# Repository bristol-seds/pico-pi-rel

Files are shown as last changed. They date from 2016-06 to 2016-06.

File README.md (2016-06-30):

# pico-pi

This repository contains the source and hardware for a High Altitude
Balloon (HAB) tracker based around a
[Raspberry Pi Zero](https://www.raspberrypi.org/products/pi-zero/). The
Pi Zero V1.3 includes a camera connector, so we can use a
[Sony IMX219 camera](https://uk.farnell.com/raspberry-pi/rpi-8mp-camera-board/raspberry-pi-camera-board-v2/dp/2510728)
to return live images.

This design is optimised for weight-constrained payloads that use
solar panels for power. If you're new to HAB or using a Latex weather
balloon, then check out the awesome
[Pi in the Sky](http://www.pi-in-the-sky.com) project instead!

# Hardware

[README.md](hw/README.md)

# Mass Budget

| Part | Mass |
| ---  | --- |
| Raspberry Pi Zero V1.3 | 9g |
| Raspberry Pi Camera | 3.5g |
| [5F Supercap](http://www.farnell.com/datasheets/1640988.pdf) | 7g |
| Solar panels to supply 400mA @ 4.8V | 15.2g |
| [pico-pi hardware](hw/) | 8g |
| Thermal insulation | 3g |
| Wire for antennas | 3g |

Current Total: `48.7g`
Target: `50g`

# License

[MIT](LICENSE.md)

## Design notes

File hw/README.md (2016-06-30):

# Hardware for pico-pi

The folder contains the schematic files for the pico-pi header
board. This provides us with the all the additional hardware
functionality we need for a balloon tracker.

* 868MHz RFM96W LoRa Radio
* u-Blox MAX-M8Q GPS
* 144MHz and 434MHz Radios
* Microcontroller to act as watchdog
* Input diodes for solar panels
* optional ADXL345 accelerometer

_[Schematics](pico-pi.sch.pdf)_

_[Board Drawings](pico-pi.kicad_pcb.pdf)_

_[3D Rendering](pico-pi.kicad_pcb.png)_

_[Gerbers](gerbers/)_

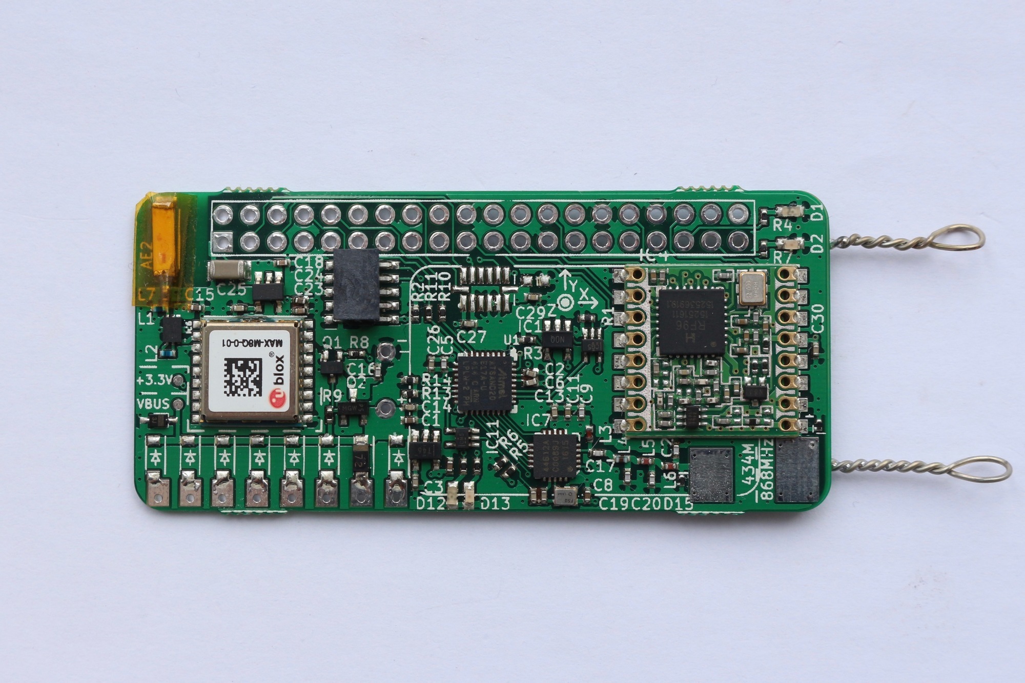
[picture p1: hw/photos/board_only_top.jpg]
Assembled pico-pi header board


# Design Features

## GPS Amplifier + Antenna

We include a GPS
[Front End](http://www.infineon.com/dgdl/bgm1034N7.pdf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)
and a
[Chip Antenna](http://www.johansontechnology.com/datasheets/antennas/1575AT43A0040.pdf). This
choice of antenna trades off sensitivity for low mass, while the Front
End mantains sufficient sensitivity and noise rejection.

## Power Conditioning

Pi Zero uses a
[PAM2306](http://www.mouser.com/ds/2/115/PAM2306-336770.pdf) for
power. Specifically it uses the KE variant for both 1.8V and 3.3V
outputs. The camera supply comes from this 3.3V line.

We can reduce the voltage on the 5V net to about 3.5V as we're not
using either the HDMI or USB sockets. This avoids having to include a
boost regulator, which saves cost and complexity.

A [supercapacitor](http://www.farnell.com/datasheets/1640988.pdf)
prevents voltage droop and brown-out in periods of high demand or
momentary solar panel shadowing. This allows us to use fewer solar
panels, and means we don't need to profile maximum current
consumption.

The Atmel SAMD20 microcontroller enables power to the rest of the
system, and also acts as watchdog. The GPS and RFM95W radio are
supplied by their own 3.3V LDO to reduce the load on the pi zero buck.

## ADXL345

Accelerometer data might be useful, in particular it will give us
pitch when taking photos. Could also be processed to quantify 'turbulence'.

The
[ADXL345](http://www.analog.com/media/en/technical-documentation/data-sheets/ADXL345.pdf)
is an Aerospace Grade part with many common libraries.

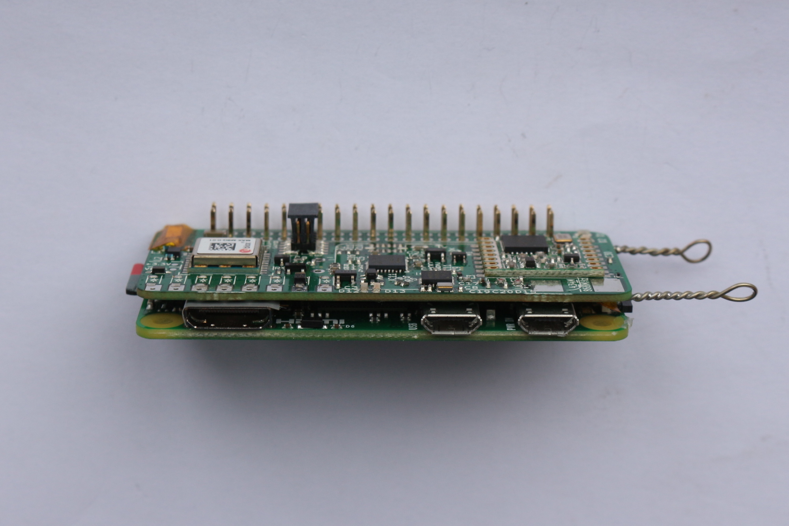
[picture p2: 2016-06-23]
hw/photos/pico-pi-side.jpg

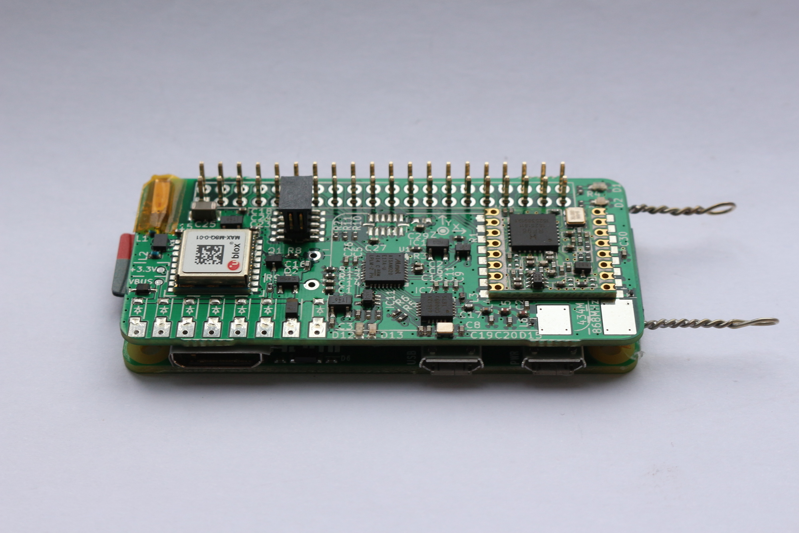
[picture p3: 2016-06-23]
hw/photos/pico-pi-top-side.jpg

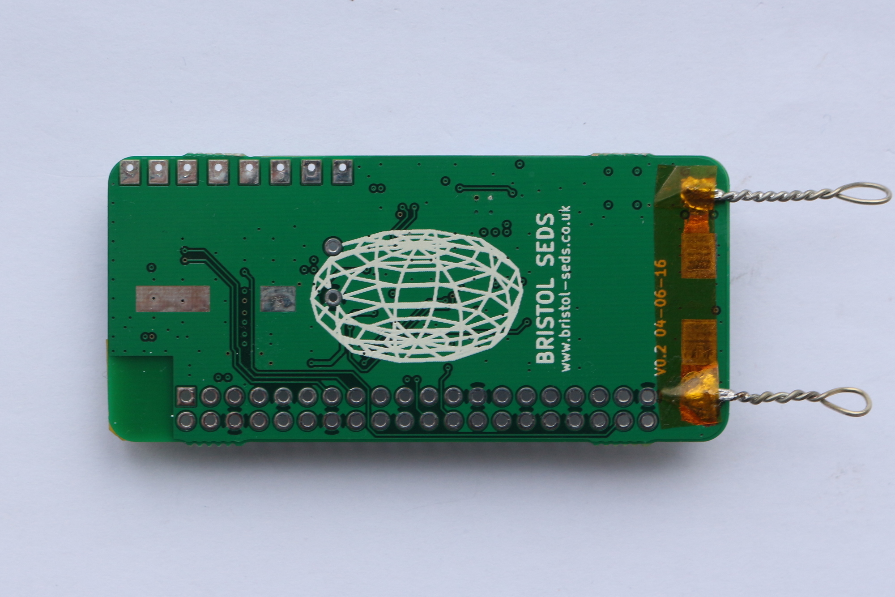
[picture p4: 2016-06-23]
hw/photos/board_only_bottom.jpg

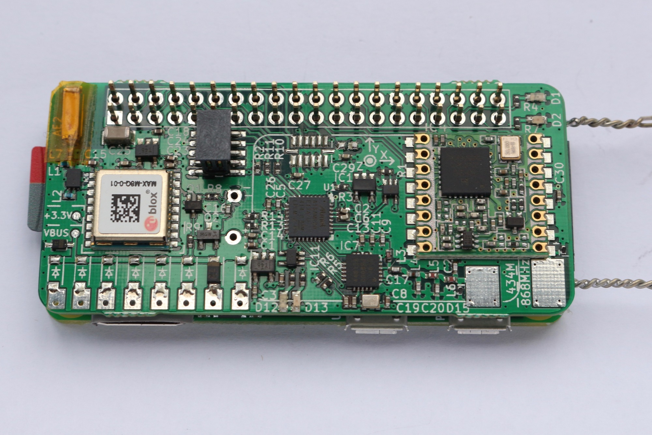
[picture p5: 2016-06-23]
hw/photos/pico-pi-top-side2.jpg

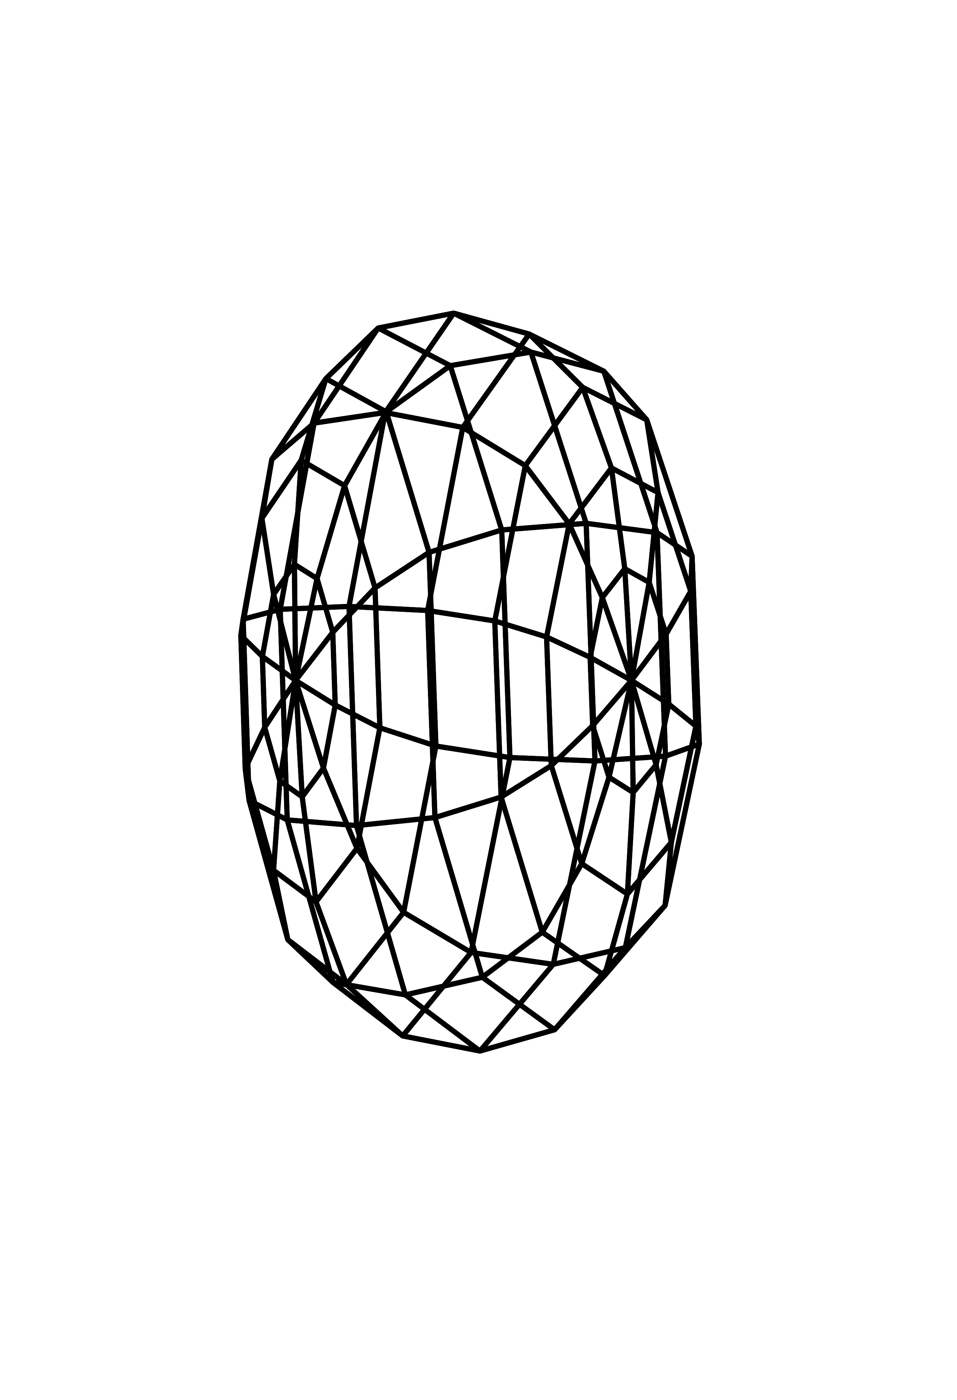
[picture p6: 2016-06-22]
hw/wireframe.png

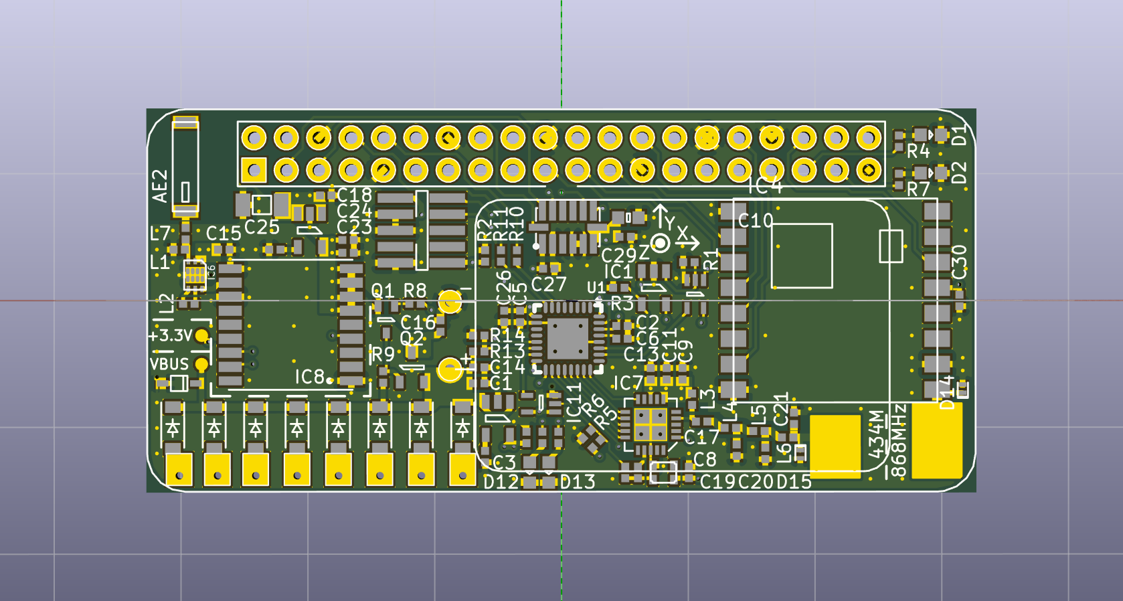
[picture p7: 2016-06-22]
hw/pico-pi.kicad_pcb.png

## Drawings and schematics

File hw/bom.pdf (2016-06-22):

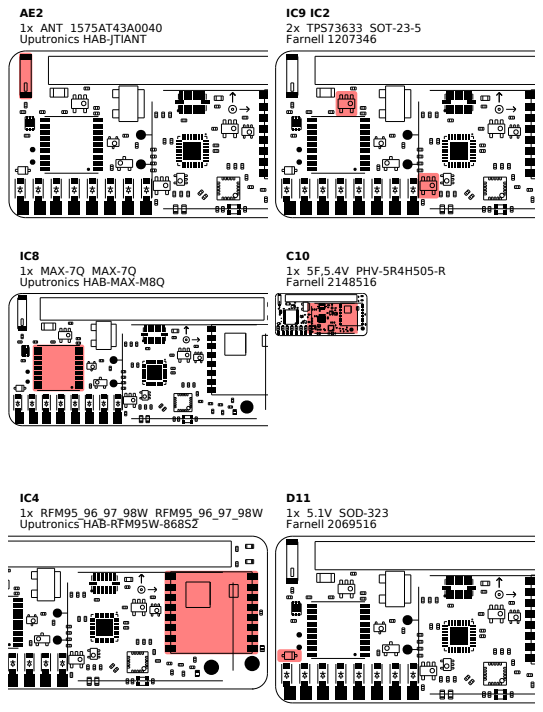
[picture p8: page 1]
AE2 1x ANT 1575AT43A0040 Uputronics HAB-JTIANT; IC4 1x RFM95_96_97_98W RFM95_96_97_98W Uputronics HAB-RFM95W-868S2; IC9 IC2 2x TPS73633 SOT-23-5 Farnell 1207346; C10 1x 5F,5.4V PHV-5R4H505-R Farnell 2148516; D11 1x 5.1V SOD-323 Farnell 2069516

1x MAX-7Q MAX-7Q
Uputronics HAB-MAX-M8Q

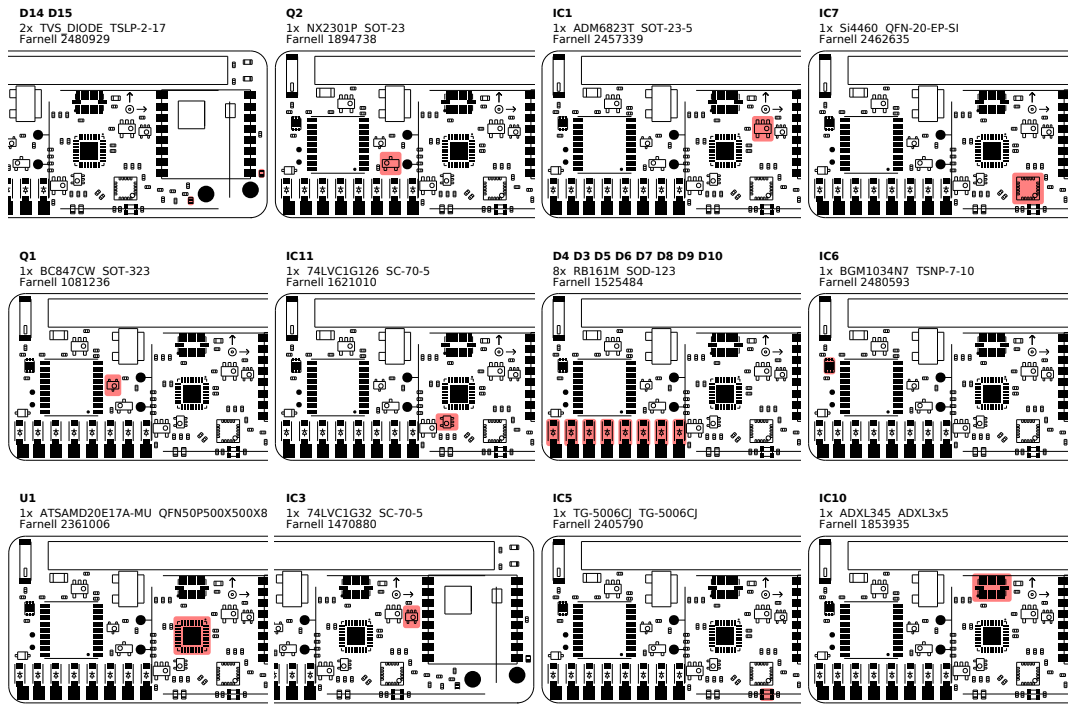
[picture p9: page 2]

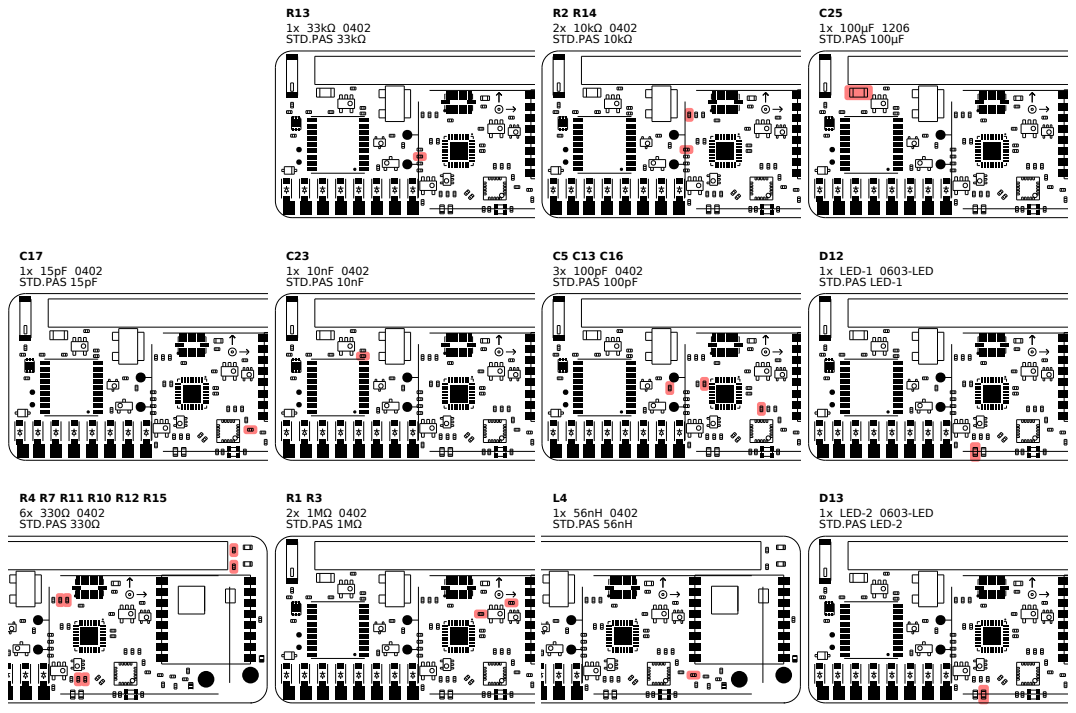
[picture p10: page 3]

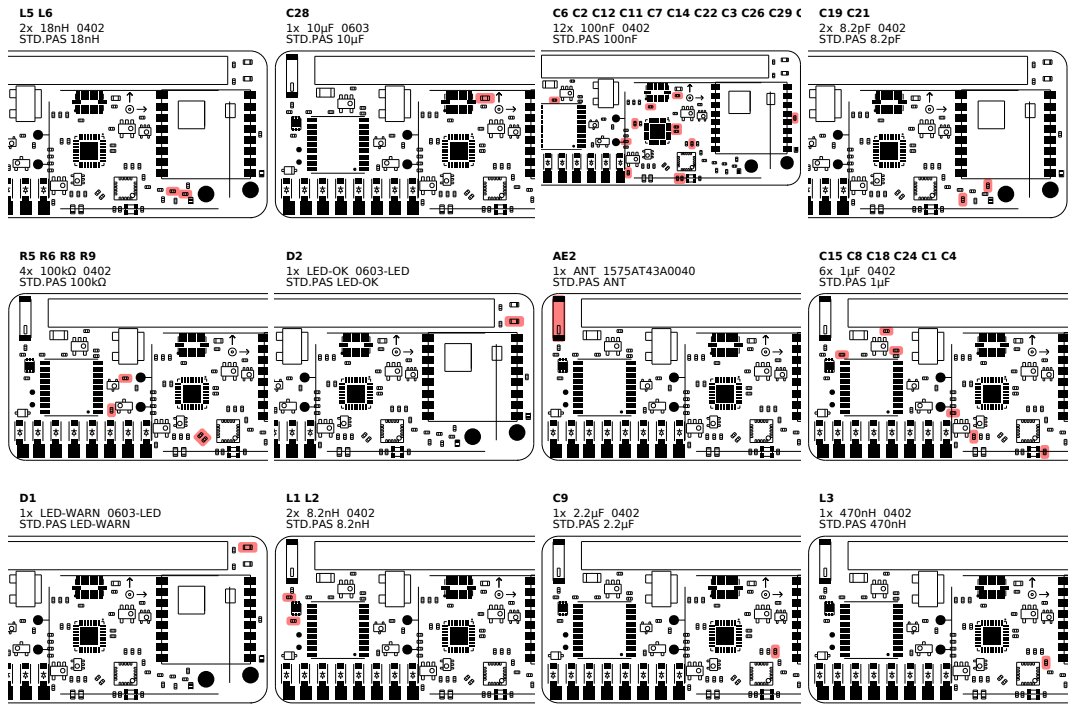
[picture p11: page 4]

1x LED-OK 0603-LED
STD.PAS LED-OK

1x LED-WARN 0603-LED
STD.PAS LED-WARN

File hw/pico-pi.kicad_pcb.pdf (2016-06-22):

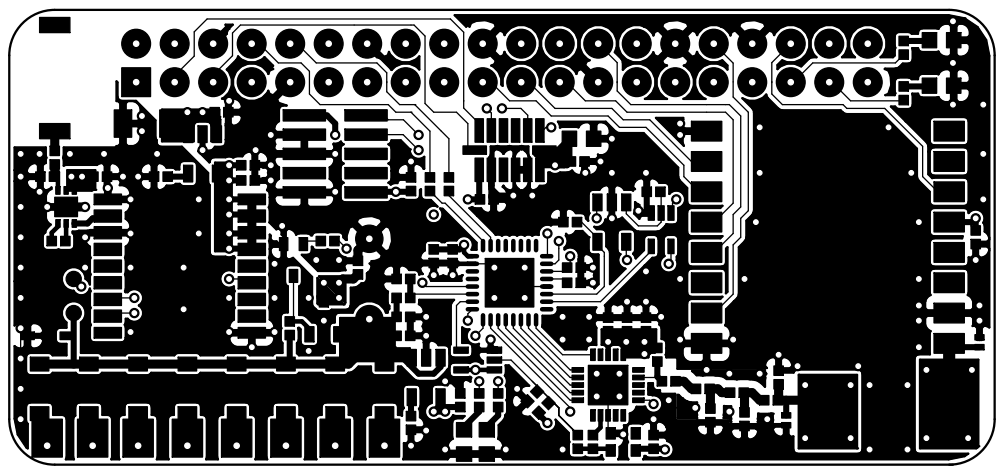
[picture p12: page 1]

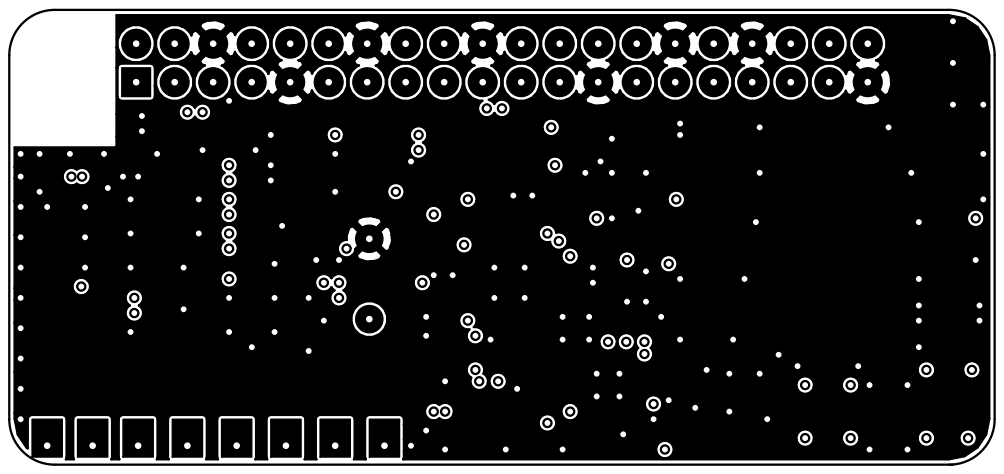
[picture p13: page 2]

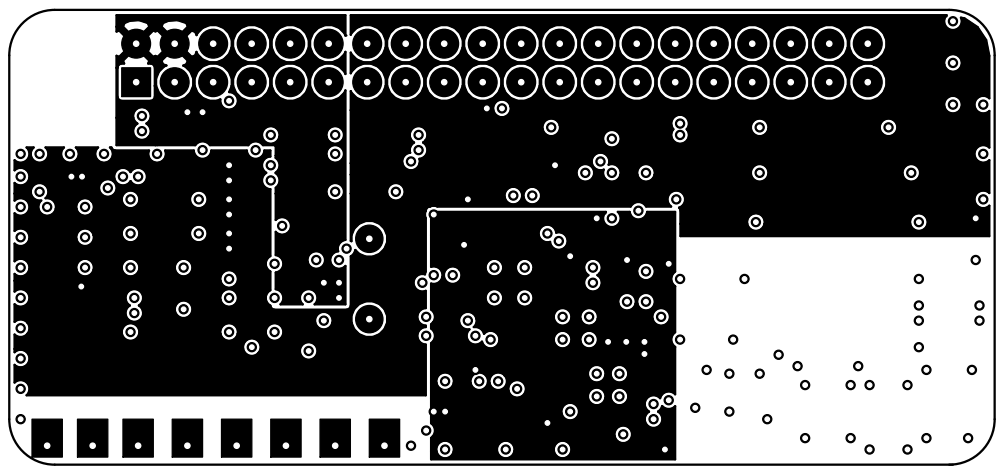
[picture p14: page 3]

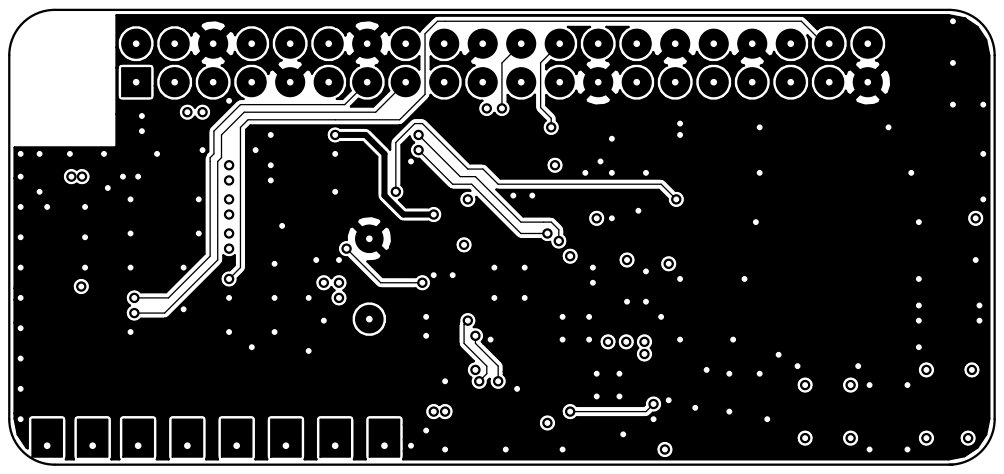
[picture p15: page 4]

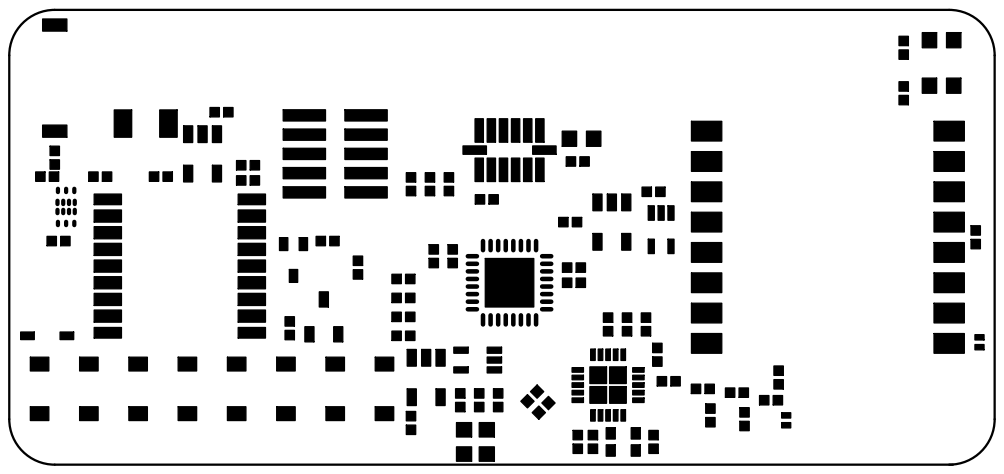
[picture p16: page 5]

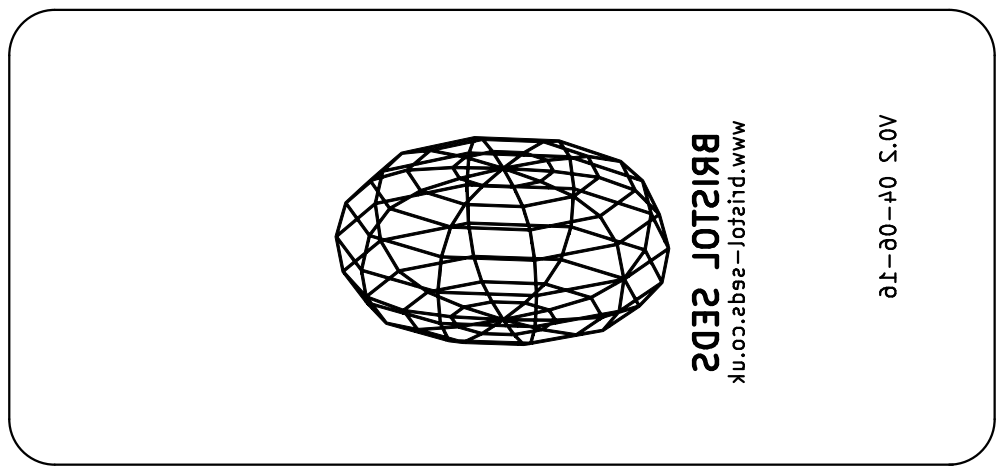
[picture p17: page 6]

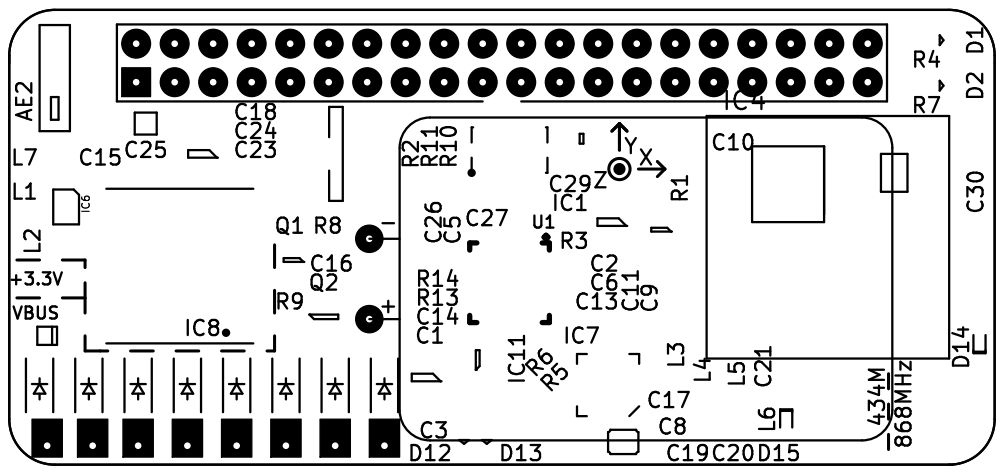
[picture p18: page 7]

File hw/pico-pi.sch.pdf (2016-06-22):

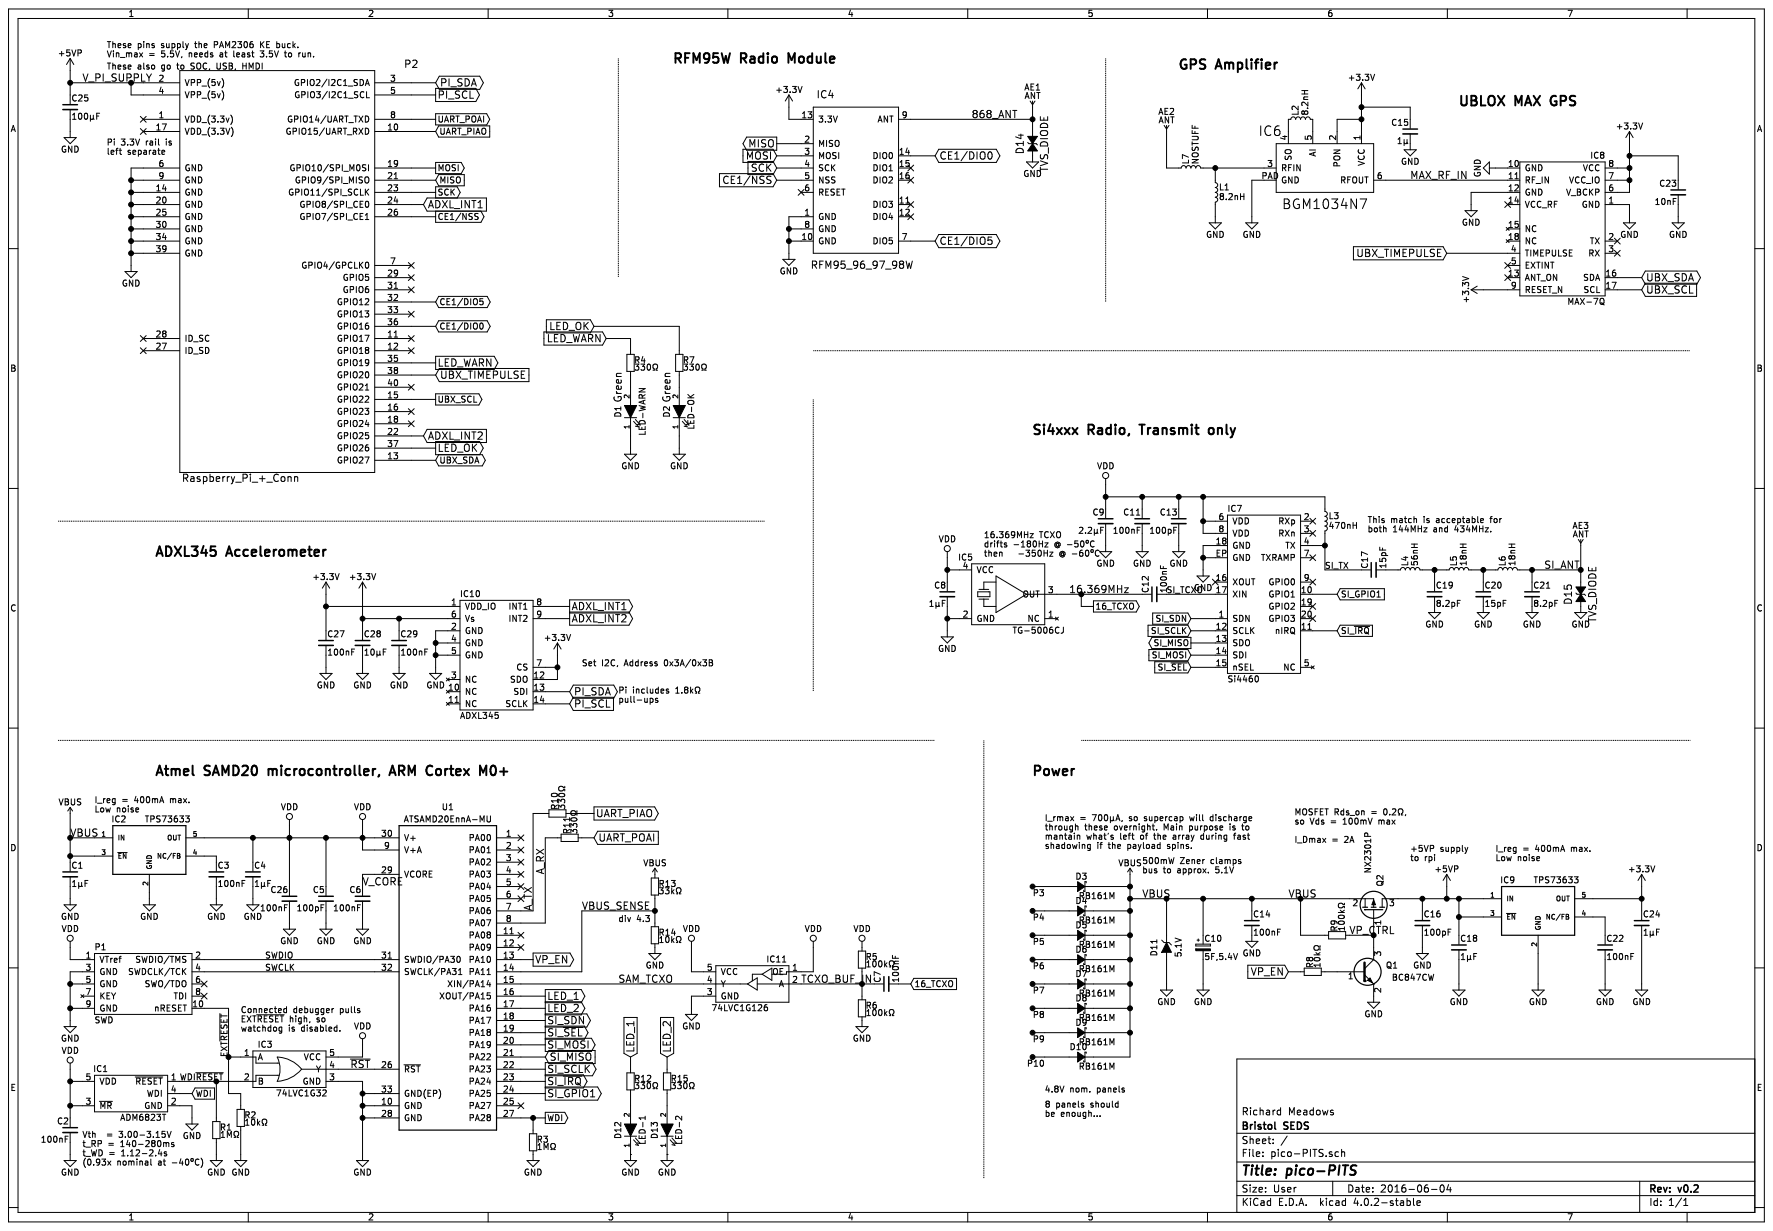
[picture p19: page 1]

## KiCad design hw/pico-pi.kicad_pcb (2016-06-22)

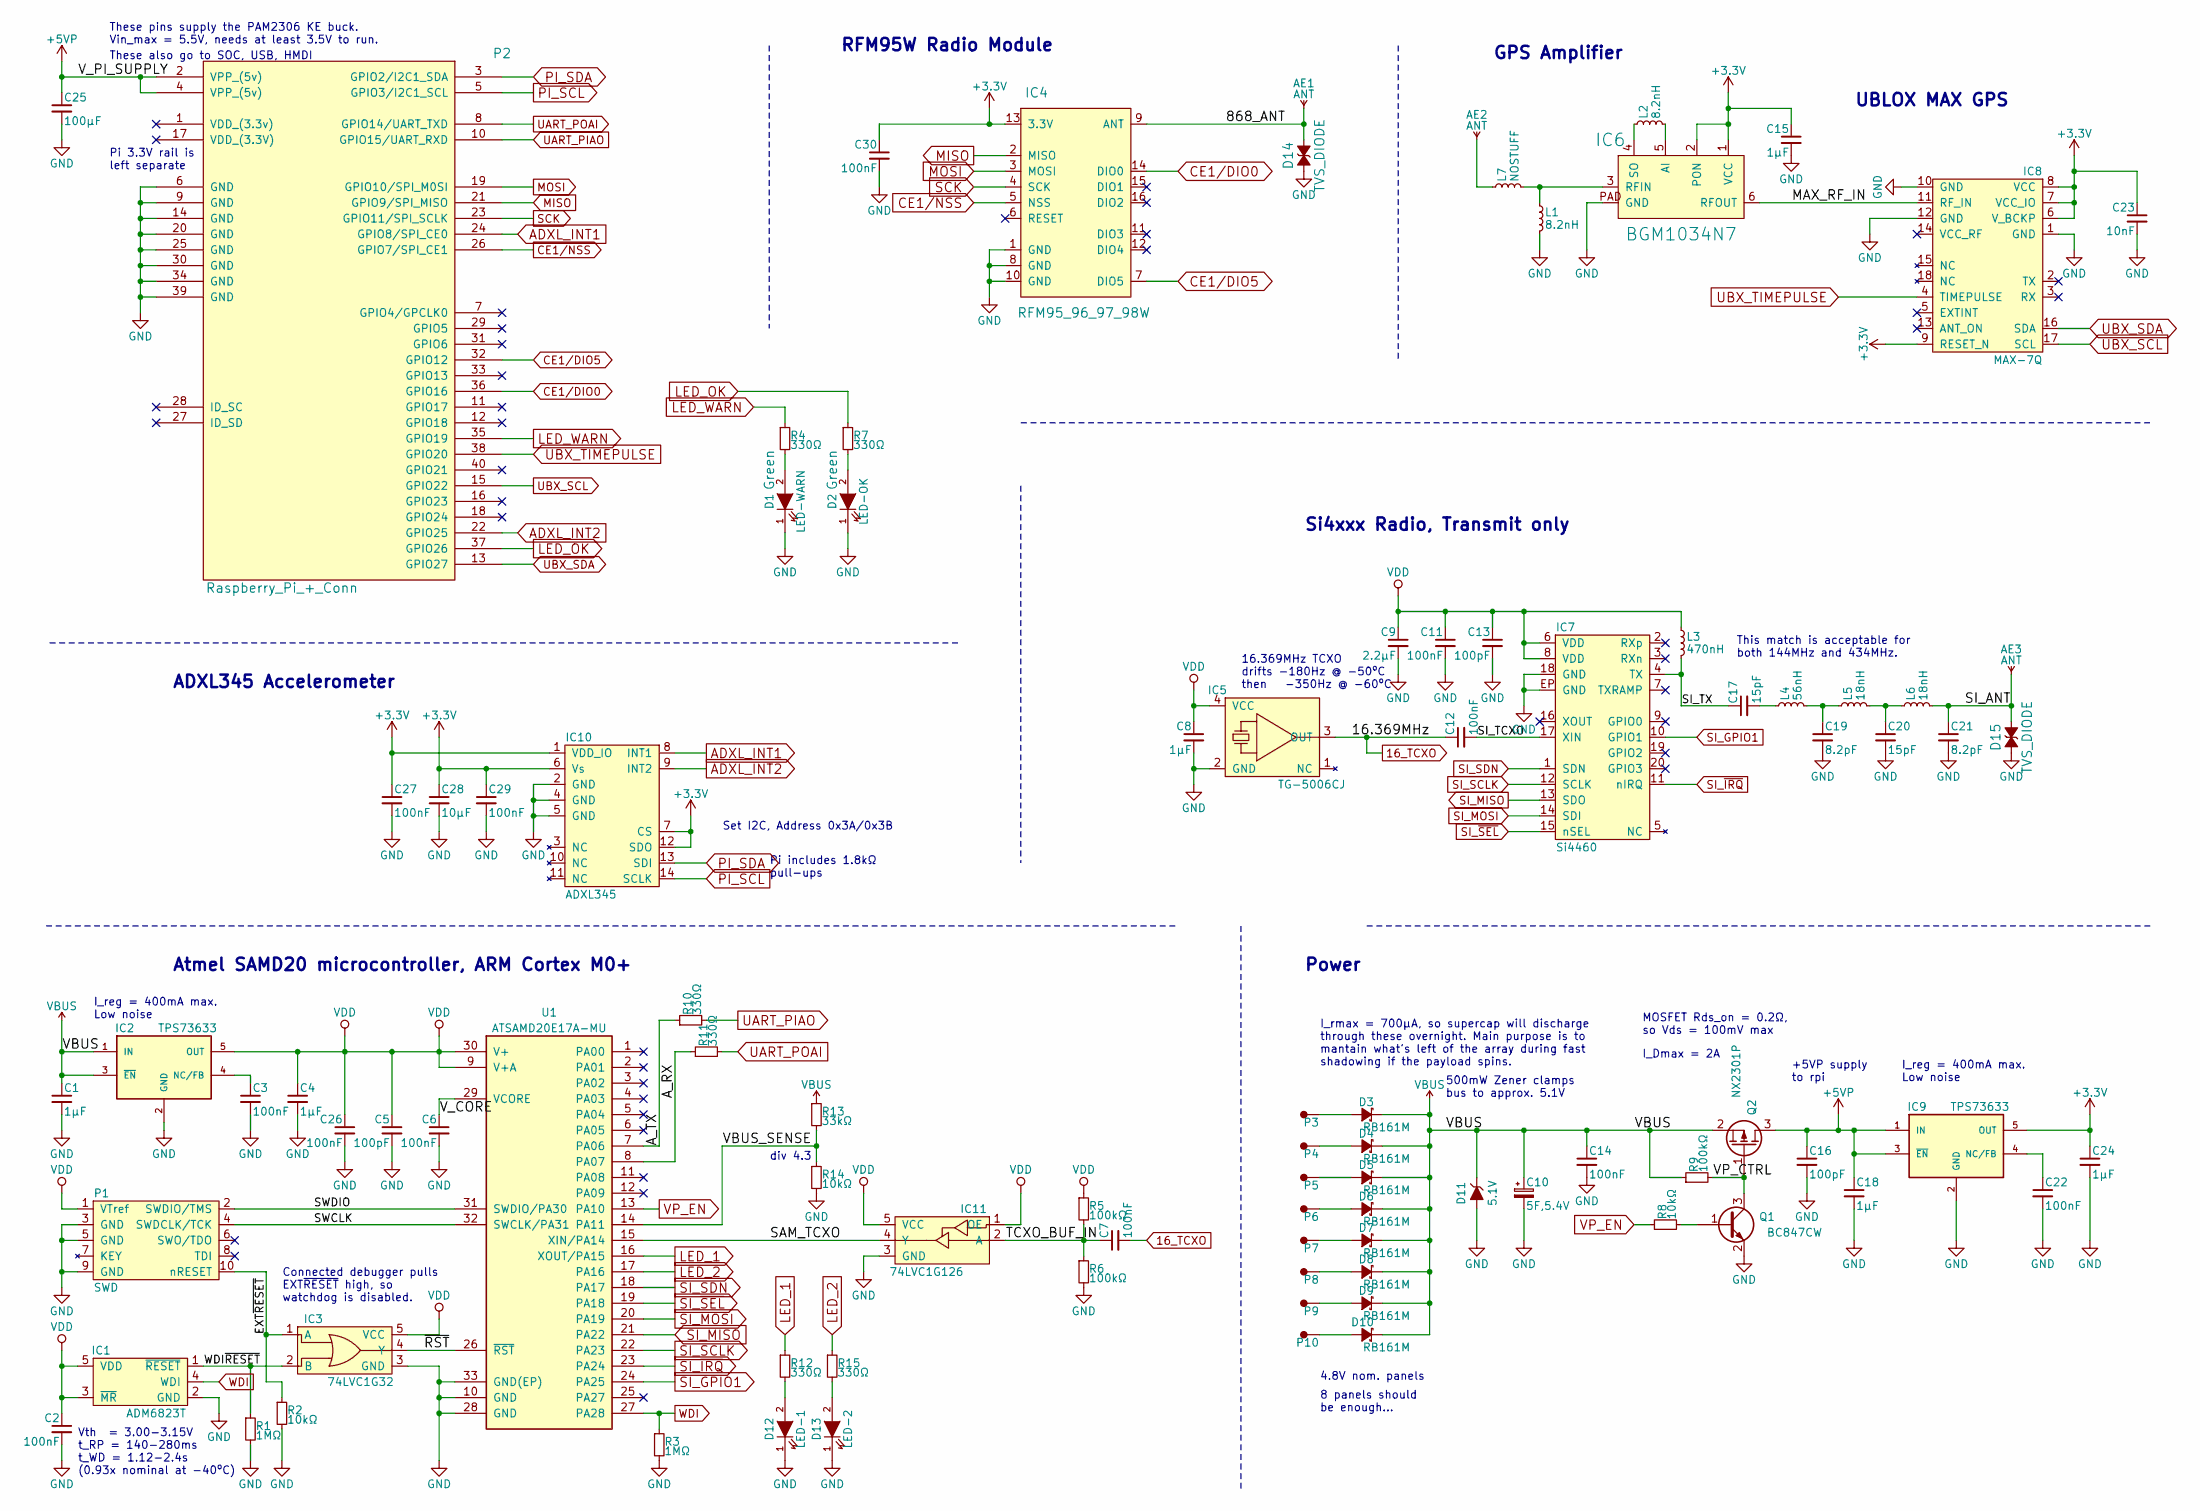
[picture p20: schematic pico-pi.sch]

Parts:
AE1, AE3: ANT; WIREPAD
AE2: ANT; 1575AT43A0040
C1, C4, C8, C15, C18, C24: 1µF; 0402
C2, C3, C6, C7, C11, C12, C14, C22, C26, C27, C29, C30: 100nF; 0402
C5, C13, C16: 100pF; 0402
C9: 2.2µF; 0402
C10: 5F,5.4V; PHV-5R4H505-R; Farnell 2148516
C17, C20: 15pF; 0402
C19, C21: 8.2pF; 0402
C23: 10nF; 0402
C25: 100µF; 1206
C28: 10µF; 0603
D1: LED-WARN; 0603-LED
D2: LED-OK; 0603-LED
D3, D4, D5, D6, D7, D8, D9, D10: RB161M; SOD-123; Farnell 1525484
D11: 5.1V; SOD-323; Farnell 2069516
D12: LED-1; 0603-LED
D13: LED-2; 0603-LED
D14, D15: TVS_DIODE; TSLP-2-17; Farnell 2480929
IC1: ADM6823T; SOT-23-5; Farnell 2457339
IC2, IC9: TPS73633; SOT-23-5; Farnell 1207346
IC3: 74LVC1G32; SC-70-5; Farnell 1470880
IC4: RFM95_96_97_98W
IC5: TG-5006CJ; Farnell 2405790
IC6: BGM1034N7; TSNP-7-10; Farnell 2480593
IC7: Si4460; QFN-20-EP-SI; Farnell 2462635
IC8: MAX-7Q
IC10: ADXL345; ADXL3x5; Farnell 1853935
IC11: 74LVC1G126; SC-70-5; Farnell 1621010
L1, L2: 8.2nH; 0402
L3: 470nH; 0402
L4: 56nH; 0402
L5, L6: 18nH; 0402
L7: NOSTUFF; 0402
P1: SWD; FTSH-105-01-L-DV-K
P2: Raspberry_Pi_+_Conn; Rasberry_Pi_Zero
P3, P4, P5, P6, P7, P8, P9, P10: PAD; 2mm_solder_pad
Q1: BC847CW; SOT-323; Farnell 1081236
Q2: NX2301P; SOT-23; Farnell 1894738
R1, R3: 1MΩ; 0402
R2, R8, R14: 10kΩ; 0402
R4, R7, R10, R11, R12, R15: 330Ω; 0402
R5, R6, R9: 100kΩ; 0402
R13: 33kΩ; 0402
U1: ATSAMD20E17A-MU; QFN50P500X500X80-33; Farnell 2361006

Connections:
16_TCXO: C7.2, C12.1, IC5.3 (OUT)
+3V3: C15.1, C23.1, C24.1, C27.1, C28.1, C29.1, C30.1, IC4.13 (3.3V), IC6.1 (VCC), IC6.2 (PON), IC8.6 (V_BCKP), IC8.7 (VCC_IO), IC8.8 (VCC), IC8.9 (RESET_N), IC9.5 (OUT), IC10.1 (VDD_IO), IC10.6 (Vs), IC10.7 (CS), IC10.12 (SDO); also elsewhere on the board
+5VP: C16.1, C18.1, C25.1, IC9.1 (IN), IC9.3 (~EN~), P2.2 (VPP_(5v)), P2.4 (VPP_(5v)), Q2.3 (D)
/868_ANT: AE1.1, D14.1, IC4.9 (ANT)
/A_RX: R11.1, U1.8 (PA07)
/A_TX: R10.1, U1.7 (PA06)
/EXT~RESET: IC3.1 (A), P1.10 (nRESET), R2.1
/MAX_RF_IN: IC6.6 (RFOUT), IC8.11 (RF_IN)
/SAM_TCXO: IC11.4 (Y), U1.15 (XIN/PA14)
/SI_ANT: AE3.1, C21.1, D15.1, L6.2
/SI_TCXO: C12.2, IC7.17 (XIN)
/SI_TX: C17.1, IC7.4 (TX), L3.2
/SWCLK: P1.4 (SWDCLK/TCK), U1.32 (SWCLK/PA31)
/SWDIO: P1.2 (SWDIO/TMS), U1.31 (SWDIO/PA30)
/TCXO_BUF_IN: C7.1, IC11.2 (A), R5.2, R6.1
/VBUS_SENSE: R13.2, R14.1, U1.14 (PA11)
/VP_CTRL: Q1.3 (C), Q2.1 (G), R9.2
/V_CORE: C6.1, U1.29 (VCORE)
/WDI~RESET: IC1.1 (~RESET), IC3.2 (B), R1.1
/~RST: IC3.4 (Y), U1.26 (~RST)
ADXL_INT1: IC10.8 (INT1), P2.24 (GPIO8/SPI_CE0)
ADXL_INT2: IC10.9 (INT2), P2.22 (GPIO25)
CE1/DIO0: IC4.14 (DIO0), P2.36 (GPIO16)
CE1/DIO5: IC4.7 (DIO5), P2.32 (GPIO12)
CE1/NSS: IC4.5 (NSS), P2.26 (GPIO7/SPI_CE1)
GND: C1.2, C2.2, C3.2, C4.2, C5.2, C6.2, C8.2, C9.2, C10.2, C11.2, C13.2, C14.2, C15.2, C16.2, C18.2, C19.2, C20.2, C21.2, C22.2, C23.2, C24.2, C25.2, C26.2, C27.2, C28.2, C29.2, C30.2, D1.1 (K), D2.1 (K), D11.2 (A), D12.1 (K), D13.1 (K), D14.2, D15.2, IC1.2 (GND), IC2.2 (GND), IC3.3 (GND), IC4.1 (GND), IC4.8 (GND), IC4.10 (GND), IC5.2 (GND), IC6.PAD (GND), IC7.18 (GND), IC7.EP (GND), IC8.1 (GND), IC8.10 (GND), IC8.12 (GND), IC9.2 (GND), IC10.2 (GND), IC10.4 (GND), IC10.5 (GND), IC11.3 (GND), L1.2, P1.3 (GND), P1.5 (GND), P1.9 (GND), P2.6 (GND), P2.9 (GND), P2.14 (GND), P2.20 (GND), P2.25 (GND), P2.30 (GND), P2.34 (GND), P2.39 (GND), Q1.2 (E), R1.2, R2.2, R3.2, R6.2, R14.2, U1.10 (GND), U1.28 (GND), U1.33 (GND(EP))
LED_1: R12.1, U1.16 (XOUT/PA15)
LED_2: R15.1, U1.17 (PA16)
LED_OK: P2.37 (GPIO26), R7.1
LED_WARN: P2.35 (GPIO19), R4.1
MISO: IC4.2 (MISO), P2.21 (GPIO9/SPI_MISO)
MOSI: IC4.3 (MOSI), P2.19 (GPIO10/SPI_M0SI)
unnamed: AE2.1, L7.1
unnamed: C3.1, IC2.4 (NC/FB)
unnamed: C17.2, L4.1
unnamed: C19.1, L4.2, L5.1
unnamed: C20.1, L5.2, L6.1
unnamed: C22.1, IC9.4 (NC/FB)
unnamed: D1.2 (A), R4.2
unnamed: D2.2 (A), R7.2
unnamed: D3.2 (A), P3.1
unnamed: D4.2 (A), P4.1
unnamed: D5.2 (A), P5.1
unnamed: D6.2 (A), P6.1
unnamed: D7.2 (A), P7.1
unnamed: D8.2 (A), P8.1
unnamed: D9.2 (A), P9.1
unnamed: D10.2 (A), P10.1
unnamed: D12.2 (A), R12.2
unnamed: D13.2 (A), R15.2
unnamed: IC6.3 (RFIN), L1.1, L7.2
unnamed: IC6.4 (SO), L2.1
unnamed: IC6.5 (AI), L2.2
unnamed: Q1.1 (B), R8.2
PI_SCL: IC10.14 (SCLK), P2.5 (GPIO3/I2C1_SCL)
PI_SDA: IC10.13 (SDI), P2.3 (GPIO2/I2C1_SDA)
SCK: IC4.4 (SCK), P2.23 (GPIO11/SPI_SCLK)
SI_GPIO1: IC7.10 (GPIO1), U1.24 (PA25)
SI_MISO: IC7.13 (SDO), U1.21 (PA22)
SI_MOSI: IC7.14 (SDI), U1.20 (PA19)
SI_SCLK: IC7.12 (SCLK), U1.22 (PA23)
SI_SDN: IC7.1 (SDN), U1.18 (PA17)
SI_~IRQ: IC7.11 (nIRQ), U1.23 (PA24)
SI_~SEL: IC7.15 (nSEL), U1.19 (PA18)
UART_PIAO: P2.10 (GPIO15/UART_RXD), R10.2
UART_POAI: P2.8 (GPIO14/UART_TXD), R11.2
UBX_SCL: IC8.17 (SCL), P2.15 (GPIO22)
UBX_SDA: IC8.16 (SDA), P2.13 (GPIO27)
UBX_TIMEPULSE: IC8.4 (TIMEPULSE), P2.38 (GPIO20)
VBUS: C1.1, C10.1, C14.1, D3.1 (K), D4.1 (K), D5.1 (K), D6.1 (K), D7.1 (K), D8.1 (K), D9.1 (K), D10.1 (K), D11.1 (K), IC2.1 (IN), IC2.3 (~EN~), Q2.2 (S), R9.1, R13.1; also elsewhere on the board
VDD: C2.1, C4.1, C5.1, C8.1, C9.1, C11.1, C13.1, C26.1, IC1.3 (~MR), IC1.5 (VDD), IC2.5 (OUT), IC3.5 (VCC), IC5.4 (VCC), IC7.6 (VDD), IC7.8 (VDD), IC11.1 (OE), IC11.5 (VCC), L3.1, P1.1 (VTref), R5.1, U1.9 (V+A), U1.30 (V+)
VP_EN: R8.1, U1.13 (PA10)
WDI: IC1.4 (WDI), R3.1, U1.27 (PA28)

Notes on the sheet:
UBLOX MAX GPS
RFM95W Radio Module
GPS Amplifier
Pi 3.3V rail is left separate
Vth = 3.00-3.15V t_RP = 140-280ms t_WD = 1.12-2.4s (0.93x nominal at -40ºC)
Connected debugger pulls EXT~RESET~ high, so watchdog is disabled.
16.369MHz TCXO drifts -180Hz @ -50ºC then -350Hz @ -60ºC
Si4xxx Radio, Transmit only
I_rmax = 700µA, so supercap will discharge through these overnight. Main purpose is to mantain what's left of the array during fast shadowing if the payload spins.
8 panels should be enough...
These pins supply the PAM2306 KE buck. Vin_max = 5.5V, needs at least 3.5V to run.
These also go to SOC, USB, HMDI
4.8V nom. panels
500mW Zener clamps bus to approx. 5.1V
MOSFET Rds_on = 0.2Ω, so Vds = 100mV max
I_Dmax = 2A
This match is acceptable for both 144MHz and 434MHz.
I_reg = 400mA max. Low noise
div 4.3
Set I2C, Address 0x3A/0x3B
Pi includes 1.8kΩ pull-ups
+5VP supply to rpi
Atmel SAMD20 microcontroller, ARM Cortex M0+
Power
ADXL345 Accelerometer

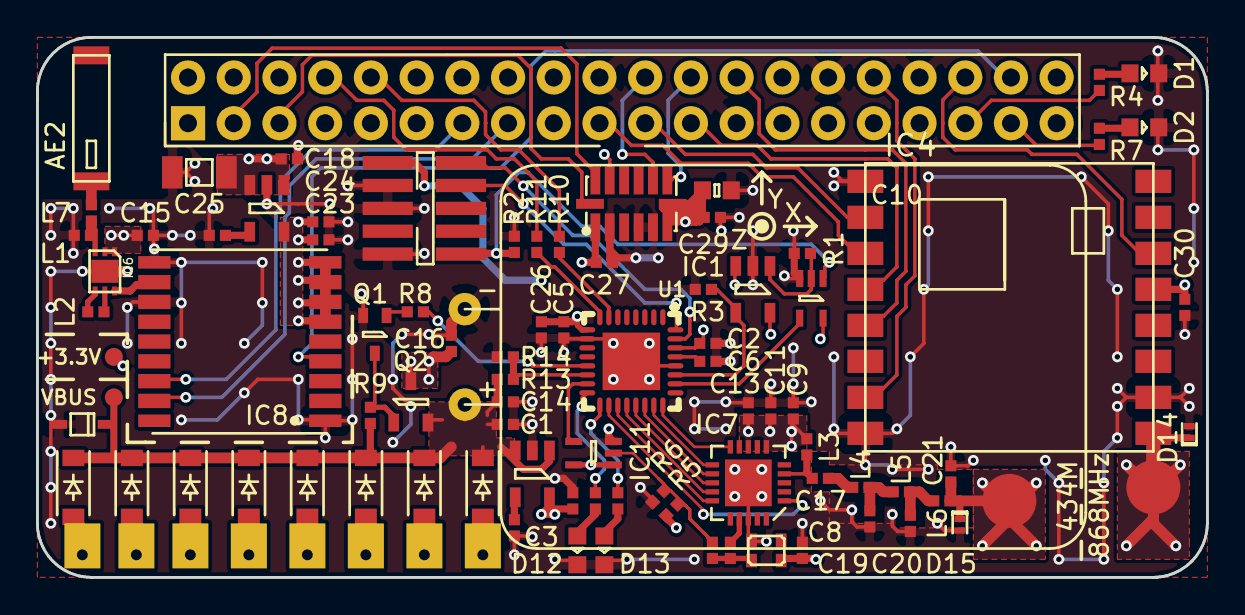
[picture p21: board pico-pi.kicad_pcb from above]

Board: 4 copper layers, 65.0 x 30.0 mm, 96 parts (0 on the bottom side), 73 nets.

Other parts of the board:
TP1, TP2: TESTPAD

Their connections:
+3V3: TP2.1; also elsewhere on the board
VBUS: TP1.1; also elsewhere on the board
